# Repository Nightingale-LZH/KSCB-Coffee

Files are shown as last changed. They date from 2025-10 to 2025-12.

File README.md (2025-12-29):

# Precision Cold Drip Coffee Maker

Alternative Interpretation of Kyoto-Style Cold Brew.

Name the coffee maker as Precision Cold Drip (still looking for better name).

## Bill of Material

### 3D-Printed Parts

The project file (.3mf) for [PrusaSlicer](https://www.prusa3d.com/page/prusaslicer_424/) are provided.

- Cold brew machine: [KSCB-3DModel/KSCB-PrusaSlicer.3mf](KSCB-3DModel/KSCB-PrusaSlicer.3mf)
- Cold brew machine case: [KSCB-3DModel/KSCB-Case-PrusaSlicer.3mf](KSCB-3DModel/KSCB-Case-PrusaSlicer.3mf)
- [Optional] STEP file for blank front place for modification: [KSCB-3DModel/BlankFrontPlate.step](KSCB-3DModel/BlankFrontPlate.step)

### Pruchased Parts

Note: in case the exact components cannot be sourced, a [STEP file](KSCB-3DModel/BlankFrontPlate.step) of blank front plate is provided for modification in `KSCB-3DModel` folder.

- **Buck-Boost Converter** (x1)
  - Any boost converter that convert 5V to 12V works. The current requirement is 1A at 12V, but regular operating amperage should never exceed that.
- **Motor Controller** (x1)
  - L298N should suffice. Other equivalent should also work.
  - PWM capability is not required. I found the PWM is not reliable enough and often stall the peristaltic pump. So, short pulsing is more consistent than continuous dripping using PWM.
  - The 5V power supply is not necessary either. If the voltage of the main power source is stable (this is often true from power bank), it can directly power the microcontroller and other 5V devices.
- **7 Segmented Display** (x1)
  - TM1637 powered module would be the best.
- **Button** (x4)
  - Any normally open momentary switch would work here.
  - The model is based on 7mm panel mount buttons.
- **LED** and **Resistor** (x5)
  - The most basic LED will work here.
  - The resistor is for current limiting. The resistance ranging from 200 ohm to 400 ohm would work. 
- **Arduino Nano** (x1)
  - Any microcontroller would work here with pinout modification. The libraries in the code are based on Arduino Framework, and written with PlatformIO extension in VSCode.
  - The code is based on Arduino Nano, and would work without any modification.
- **Peristaltic Pump** (x1)
  - A 12V small peristaltic pump with tube size 3mm ID x 5mm OD would work here. The link to the purchase page is likely to expire in the future, so source the similar item. The picture of the pump used in this build is [here](Others/PumpScreenshot.png). 

## Pump Pulse Flow Rate Calibration Data

function of best fit: 

$$R(t) = 0.000513 e^{-0.009825t} + 0.001392$$

- $t$ is the duration of pulse in milliseconds
- $R$ is the pump flow rate in grams per millisecond

The flow rate is calculated with supply voltage of 12V to L298N module. The voltage received by pump motor is around 10V according to L298N datasheet (voltage drop is around 2V).

See more detail in [KSCB-PumpCalibrationData/PumpTesting.ipynb](KSCB-PumpCalibrationData/PumpTesting.ipynb).

## System Reference Diagram

### Block Diagram

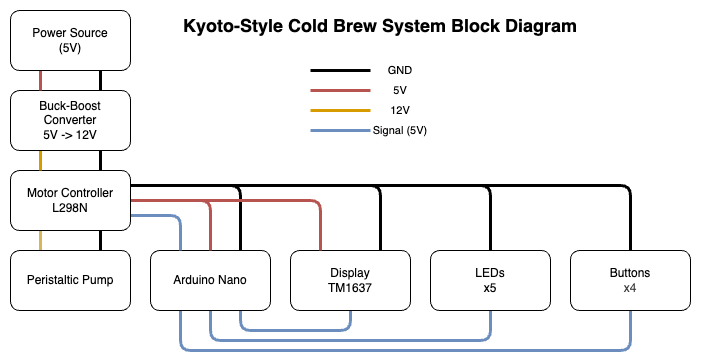
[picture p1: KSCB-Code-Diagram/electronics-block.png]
Block Diagram


### System Finite State Machine

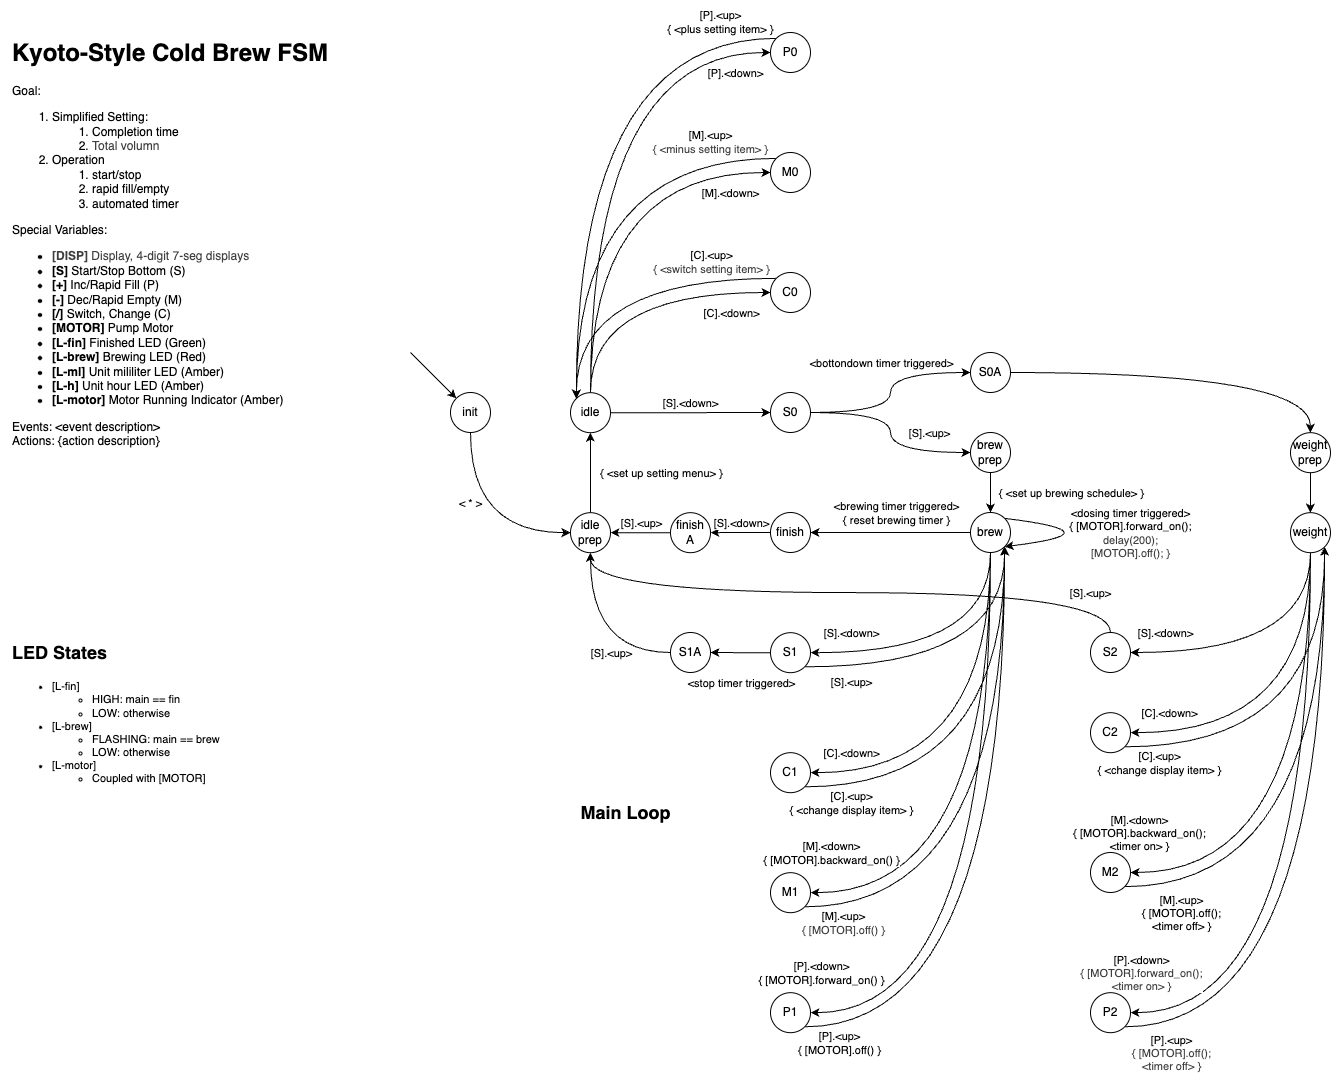
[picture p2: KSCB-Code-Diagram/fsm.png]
System Finite State Machine


## TODO

- [x] Bill of Material
- [ ] Building Guide
- [x] Model parts
- [ ] Circuit Diagram / Schematics
- [x] Calibration code/data
- [x] Control Code
- [ ] User Manual

## Credit

**Zihui(Andy) Liu** ([Personal Website](https://nightingale-lzh.github.io), [GitHub](<https://github.com/Nightingale-LZH>))

This project is published under GNU General Public License version 3 (GPLv3) which allows users to run, modify, and distribute software while ensuring that any modified versions remain open source. This project is funded by creator's love to coffee.

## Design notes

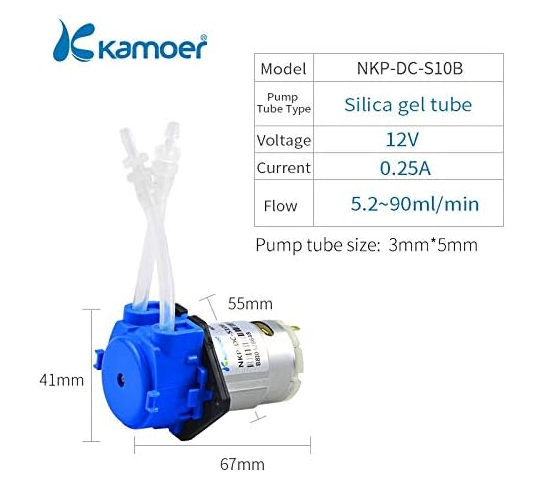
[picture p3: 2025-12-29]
Others/PumpScreenshot.png

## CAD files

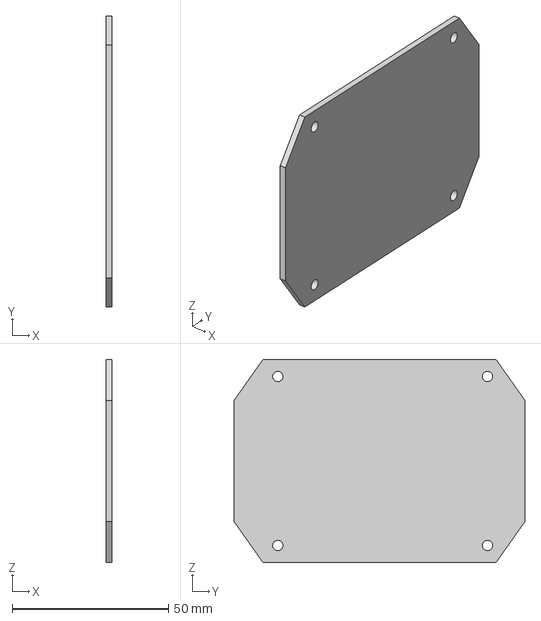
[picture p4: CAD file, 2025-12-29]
KSCB-3DModel/BlankFrontPlate.step
2.00 x 93.0 x 65.0 mm

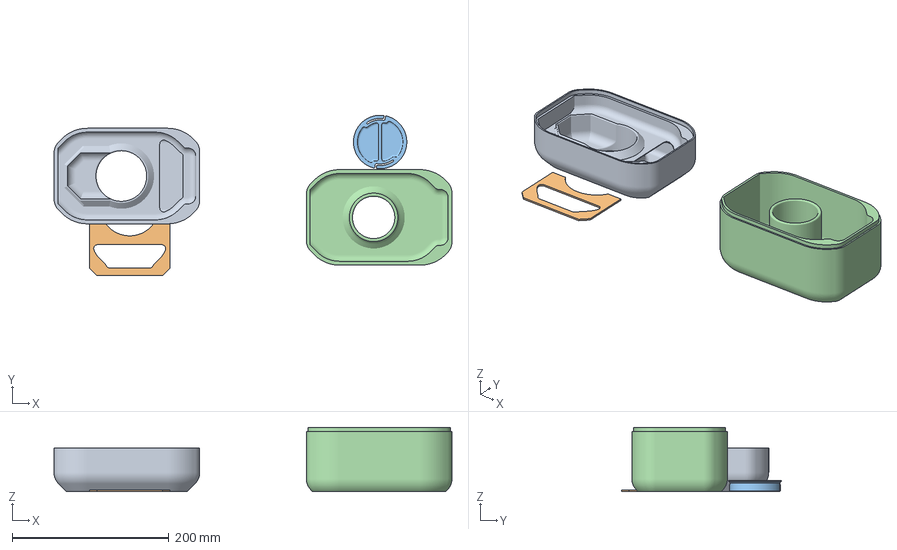
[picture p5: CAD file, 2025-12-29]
KSCB-3DModel/KSCB-Case-PrusaSlicer.3mf
508.1 x 204.8 x 82.0 mm
V1 EC Top.stl
V1 Top Insert.stl
V1 Vent Cap.stl
V1 EC Base.stl

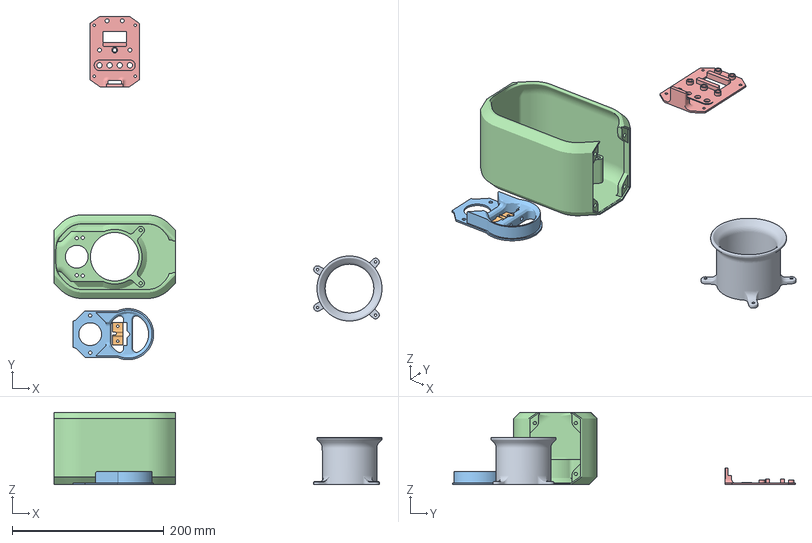
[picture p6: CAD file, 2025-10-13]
KSCB-3DModel/KSCB-PrusaSlicer.3mf
432.3 x 452.6 x 95.0 mm
V1 InnerTube.stl
V1 OverhangBrace.stl
V1 OverhangInsert.stl
V1 Shell.stl
V1 FrontPlateLayout1.stl

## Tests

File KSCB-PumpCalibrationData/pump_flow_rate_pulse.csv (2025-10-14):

on_delay_ms | n_pulse | weight_g
100 | 20 | 3.25
200 | 20 | 5.80
300 | 20 | 8.54
400 | 20 | 11.05
500 | 20 | 13.88
600 | 20 | 16.5
700 | 20 | 19.4
800 | 20 | 22.00
900 | 20 | 24.56
1000 | 20 | 27.00
100 | 40 | 6.11
200 | 40 | 10.8
200 | 40 | 11.69
300 | 40 | 17.28
100 | 40 | 6.26
100 | 40 | 6.85
100 | 40 | 6.27
200 | 40 | 11.52
200 | 40 | 10.75
200 | 40 | 11.25
300 | 40 | 17.34
300 | 40 | 17.39
300 | 40 | 16.9
400 | 20 | 11.26
400 | 20 | 11
400 | 20 | 11.25
400 | 20 | 10.78
500 | 20 | 14.10
500 | 20 | 13.7
500 | 20 | 14.12
500 | 20 | 14.07
600 | 20 | 16.92
600 | 20 | 16.6
600 | 20 | 16.82
600 | 20 | 16.17
700 | 20 | 18.90
700 | 20 | 19.52
700 | 20 | 19.64
700 | 20 | 19.42
800 | 20 | 21.25
800 | 20 | 22.19
800 | 20 | 22.33
800 | 20 | 22.76
900 | 20 | 26.12
900 | 20 | 25.50
900 | 20 | 25.66
900 | 20 | 25.80
1000 | 20 | 29.00
1000 | 20 | 28.45
1000 | 20 | 28.46
1000 | 20 | 28.42
150 | 40 | 9.14
150 | 40 | 9.15
150 | 40 | 9.10
150 | 40 | 9.05
150 | 40 | 9.16
50 | 40 | 3.50
50 | 40 | 3.60
50 | 40 | 3.40
50 | 40 | 3.42
50 | 40 | 3.34
25 | 40 | 1.75
25 | 40 | 1.88
25 | 40 | 1.68
25 | 40 | 1.75
25 | 40 | 1.82
250 | 40 | 14.47
250 | 40 | 14.65
250 | 40 | 14.46
250 | 40 | 14.50
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

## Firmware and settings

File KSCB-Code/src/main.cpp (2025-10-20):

#include "main.h"

#ifdef MAIN

void setup() {}

void loop() {
    main_loop_update();
    built_in_led_update();
    display_manager.update();
    pump_manager.update();

    delay(FSM_DELAY_MS);
}


//  +---------------------------------------------------------------------------------------------+
//  |                                          Main Loop                                          |
//  +---------------------------------------------------------------------------------------------+


void main_loop_update() {
    SETUP_FSM_FUNCTION(main_loop);

    STATE(ML_init) {
        display_manager.show_segment(SEG_PCD);
        SLEEP_TO(1000, ML_init_2);
    }

    STATE(ML_init_2) {
        display_manager.show_segment(SEG_ZLIU);
        SLEEP_TO(1500, ML_idle_prep);
    }

    //  ------- Idle -------
    STATE(ML_idle_prep) {
        pump_manager.end_schedule();
        display_manager.show_segment(SEG_empty_str);
        SLEEP_TO(500, ML_idle_prep_2);
    }

    STATE(ML_idle_prep_2) {
        pump_manager.end_schedule();
        display_manager.show_segment(SEG_PREP);
        SLEEP_TO(1000, ML_idle_prep_3);
    }

    STATE(ML_idle_prep_3) {
        //  Setting up menu
        is_setting_volumn = false;
        is_setting_time = true;

        refresh_display_menu();
        TO(ML_idle);
    }

    STATE(ML_idle) {
        refresh_display_menu_scheduled();
        WHEN(btn_change.is_pressed()) TO(ML_C0);
        WHEN(btn_plus  .is_pressed()) TO(ML_P0);
        WHEN(btn_minus .is_pressed()) TO(ML_M0);
        WHEN(btn_start .is_pressed()) { 
            display_manager.show_segment(SEG_BREW);
            RESET_TIMER(main_loop); 

            TO(ML_S0); 
        }
    }

    STATE(ML_C0) {
        WHEN(btn_change.is_released()) {
            //  switching setting item
            if (is_setting_volumn) {
                is_setting_volumn = false;
                is_setting_time = true;

            } else if (is_setting_time) {
                is_setting_volumn = true;
                is_setting_time = false;
            }

            refresh_display_menu();
            TO(ML_idle)
        }
    }

    STATE(ML_P0) {
        WHEN(btn_plus.is_released()) {
            //  plus setting item
            if (is_setting_volumn) {
                if (brewing_volumn_ml + BREWING_VOLUMN_INCREMENT_ML < 9999) {
                    brewing_volumn_ml += BREWING_VOLUMN_INCREMENT_ML;
                }
            } else if (is_setting_time) {
                if (brewing_time_mins + BREWING_TIME_INCREMENT_MINS < 99 * 60) {
                    brewing_time_mins += BREWING_TIME_INCREMENT_MINS;
                }
            }

            refresh_display_menu();
            TO(ML_idle)
        }
    }

    STATE(ML_M0) {
        WHEN(btn_minus.is_released()) {
            //  minus setting item
            if (is_setting_volumn) {
                if (brewing_volumn_ml - BREWING_VOLUMN_INCREMENT_ML > 0) {
                    brewing_volumn_ml -= BREWING_VOLUMN_INCREMENT_ML;
                }
            } else if (is_setting_time) {
                if (brewing_time_mins - BREWING_TIME_INCREMENT_MINS > 0) {
                    brewing_time_mins -= BREWING_TIME_INCREMENT_MINS;
                }
            }

            refresh_display_menu();
            TO(ML_idle)
        }
    }

    STATE(ML_S0) {
        WHEN(btn_start.is_released()) TO(ML_brew_prep);
        WHEN(IS_TIME_ELAPSED(main_loop, 3000)) {
            display_manager.show_segment(SEG_CALI);
            TO(ML_S0A);
        }
    }

    STATE(ML_S0A) {
        WHEN(btn_start.is_released()) TO(ML_weight_prep);
    }

    //  ------- Brewing -------

    STATE(ML_brew_prep) {
        //  setup brewing schedule
        long brewing_total_time_ms = brewing_time_mins * 60 * 1000;

        is_showing_brewing_time_left = true;
        is_showing_brewing_volumn_left = false;

        pump_manager.start_schedule(brewing_total_time_ms, brewing_volumn_ml);
        //  manually trigger time once to activate flashing dots
        display_manager.show_time_min(pump_manager.get_brewing_time_remaining_mim(), true, true);
        refresh_display_brewing();

        TO(ML_brew)
    }

    STATE(ML_brew) {
        refresh_display_brewing_scheduled();

        WHEN(btn_change.is_pressed()) TO(ML_C1);
        WHEN(btn_plus  .is_pressed()) { pump_manager.override_forward_on();  TO(ML_P1); }
        WHEN(btn_minus .is_pressed()) { pump_manager.override_backward_on(); TO(ML_M1); }
        WHEN(btn_start .is_pressed()) { 
            display_manager.show_segment(SEG_HOLD);
            RESET_TIMER(main_loop);     

            TO(ML_S1); 
        }
        WHEN(pump_manager.is_brewing_finished()) { 
            display_manager.show_segment(SEG_FIN);
            pump_manager.end_schedule(); 
            pump_manager.backward_on();

            SLEEP_TO(ML_finish, 15000); 
        }
    }

    STATE(ML_C1) { 
        refresh_display_brewing_scheduled();

        WHEN(btn_change.is_released()) {
            //  switching setting item
            if (is_showing_brewing_volumn_left) {
                is_showing_brewing_volumn_left = false;
                is_showing_brewing_time_left = true;

            } else if (is_showing_brewing_time_left) {
                is_showing_brewing_volumn_left = true;
                is_showing_brewing_time_left = false;
            }

            refresh_display_brewing();
            TO(ML_brew)
        }
    }

    STATE(ML_P1) {
        refresh_display_brewing_scheduled();

        WHEN(btn_plus.is_released()) {
            pump_manager.override_off();
            pump_manager.end_override();

            refresh_display_brewing();
            TO(ML_brew)
        }
    }

    STATE(ML_M1) {
        refresh_display_brewing_scheduled();

        WHEN(btn_minus.is_released()) {
            pump_manager.override_off();
            pump_manager.end_override();

            refresh_display_brewing();
            TO(ML_brew)
        }
    }

    STATE(ML_S1) {
        WHEN(btn_start.is_released()) {
            refresh_display_brewing();

            TO(ML_brew);
        }
        WHEN(IS_TIME_ELAPSED(main_loop, 3000)) { 
            display_manager.show_segment(SEG_STOP);
            pump_manager.end_schedule(); 

            TO(ML_S1A); 
        }
    }

    STATE(ML_S1A) {
        WHEN(btn_start.is_released()) TO(ML_idle_prep);
    }

    STATE(ML_finish) {
        pump_manager.off();
        led_brew.off();
        led_fin.on();

        TO(ML_finish_2)
    }

    STATE(ML_finish_2) {
        WHEN(btn_start.is_pressed()) TO(ML_finish_A);
    }

    STATE(ML_finish_A) {
        WHEN(btn_start.is_released()) TO(ML_idle_prep);
    }

    //  ------- Weighting -------

    STATE(ML_weight_prep) {
        curr_volumn_ul = 0;
        refresh_display_meansuring(curr_volumn_ul);

        TO(ML_weight)
    }

    STATE(ML_weight) {
        refresh_display_meansuring_scheduled(curr_volumn_ul);

        WHEN(btn_change.is_pressed()) TO(ML_C2);

        WHEN(btn_plus  .is_pressed()) { 
            pump_manager.override_forward_on();  
            RESET_TIMER(main_loop_measuring); 
            
            TO(ML_P2); 
        }

        WHEN(btn_minus .is_pressed()) { 
            pump_manager.override_backward_on(); 
            RESET_TIMER(main_loop_measuring); 

            TO(ML_M2); 
        }

        WHEN(btn_start .is_pressed()) TO(ML_S2);
    }

    STATE(ML_C2) { 
        WHEN(btn_change.is_released()) {
            curr_volumn_ul = 0;
            refresh_display_meansuring(curr_volumn_ul);

            TO(ML_weight)
        }
    }

    STATE(ML_P2) {
        refresh_display_meansuring_scheduled(
            curr_volumn_ul + PumpStats::ms2ul(TIME_ELAPSED(main_loop_measuring))
        );

        WHEN(btn_plus.is_released()) {
            pump_manager.override_off();
            curr_volumn_ul += PumpStats::ms2ul(TIME_ELAPSED(main_loop_measuring));
            pump_manager.end_override();
            refresh_display_meansuring(curr_volumn_ul);

            TO(ML_weight)
        }
    }

    STATE(ML_M2) {
        refresh_display_meansuring_scheduled(
            curr_volumn_ul - PumpStats::ms2ul(TIME_ELAPSED(main_loop_measuring))
        );

        WHEN(btn_minus.is_released()) {
            pump_manager.override_off();
            curr_volumn_ul -= PumpStats::ms2ul(TIME_ELAPSED(main_loop_measuring));
            pump_manager.end_override();
            refresh_display_meansuring(curr_volumn_ul);

            TO(ML_weight)
        }
    }

    STATE(ML_S2) {
        WHEN(btn_start.is_released()) TO(ML_idle_prep);
    }
}

//  +---------------------------------------------------------------------------------------------+
//  |                                       Helper Function                                       |
//  +---------------------------------------------------------------------------------------------+

void refresh_display_menu() {
    if (is_setting_volumn) {
        display_manager.show_ml(brewing_volumn_ml);
    } else if (is_setting_time) {
        display_manager.show_time_min(brewing_time_mins, true, false);
    }

    led_brew.off();
    led_fin.off();
}

void refresh_display_menu_scheduled() {
    if (!IS_TIME_ELAPSED(refresh_display_menu_scheduled_timer, 500)) {
        return;
    } 
    RESET_TIMER(refresh_display_menu_scheduled_timer); 

    refresh_display_menu();
}

void refresh_display_brewing() {
    if (is_showing_brewing_time_left) {
        long time_remaining_min = pump_manager.get_brewing_time_remaining_mim();
        if (time_remaining_min < 0) { 
            time_remaining_min = 0;
            display_manager.show_time_min(0, true, false);
        }

        if (display_manager.is_showing_hr_min()) {
            display_manager.update_time_min(time_remaining_min);
        } else {
            //  now showing the time, then call the function to reset
            display_manager.show_time_min(time_remaining_min, true, true);
        }

    } else if (is_showing_brewing_volumn_left) {
        display_manager.show_ml(pump_manager.get_brewing_volumn_remaining_ml());
    }

    led_brew.on();
    led_fin.off();
}

void refresh_display_brewing_scheduled() {
    if (!IS_TIME_ELAPSED(refresh_display_brewing_scheduled_timer, 500)) {
        return;
    } 
    RESET_TIMER(refresh_display_brewing_scheduled_timer); 

    refresh_display_brewing();
}

void refresh_display_meansuring(long volumn_ul) {
    display_manager.show_ml(volumn_ul / 1000);
    led_brew.on();
    led_fin.on();
}

void refresh_display_meansuring_scheduled(long volumn_ul) {
    if (!IS_TIME_ELAPSED(refresh_display_meansuring_scheduled_timer, 100)) {
        return;
    } 
    RESET_TIMER(refresh_display_meansuring_scheduled_timer); 

    refresh_display_meansuring(volumn_ul);
}

//  +---------------------------------------------------------------------------------------------+
//  |                                        Autonomous                                           |
//  +---------------------------------------------------------------------------------------------+

void built_in_led_update() {
    SETUP_FSM_FUNCTION(builtin_led);

    STATE(0) {
        led_builtin.on();
        SLEEP_TO_NEXT(1000);
    }

    STATE(1) {
        led_builtin.off();
        SLEEP_TO(1000, 0);
    }
}

///////////////////////////////////////////////////////////////////////////////////////////////////
#elif defined(CALIBRATE)

#define ON_DURATION_MS 200
#define OFF_DURATION_MS 500
#define N_PULSE 0

void setup() {
    display.showNumberDec(0);
    
    for (int i = 0; i < N_PULSE; i++) {
        delay(OFF_DURATION_MS);
        pump.forward_on();
        led_motor.on();
        delay(ON_DURATION_MS);
        pump.off();
        led_motor.off();

        display.showNumberDec(i + 1);
    }

    led_fin.on();
}

void loop() {
    if (btn_plus.is_pressed()) {
        pump.forward_on();
        led_motor.on();
    } else if (btn_minus.is_pressed()) {
        pump.backward_on();
        led_motor.on();
    } else {
        pump.off();
        led_motor.off();
    }
    delay(100);
}

///////////////////////////////////////////////////////////////////////////////////////////////////
#elif defined(DEBUG)

//  DEBUG OPTIONS
#define DEBUG_LED
// #define DEBUG_MOTOR
// #define DEBUG_BUTTON
#define DEBUG_DISPLAY

void setup() {
    #ifdef DEBUG_MOTOR
    pinMode(PIN_L298N_ENA, OUTPUT);
    pinMode(PIN_L298N_IN1, OUTPUT);
    pinMode(PIN_L298N_IN2, OUTPUT);

    // Motor Forward Direcction
    digitalWrite(PIN_L298N_IN1, HIGH);
    digitalWrite(PIN_L298N_IN2, LOW);
    #endif  //  DEBUG_MOTOR


    #ifdef DEBUG_LED
    pinMode(PIN_LED_BUILTIN, OUTPUT);
    pinMode(PIN_LED_BREW  , OUTPUT);
    pinMode(PIN_LED_FIN   , OUTPUT);
    pinMode(PIN_LED_MOTOR , OUTPUT);
    pinMode(PIN_LED_ML    , OUTPUT);
    pinMode(PIN_LED_HR_MIN, OUTPUT);
    #endif  //  DEBUG_LED


    #ifdef DEBUG_BUTTON
    Serial.begin(9600);
    pinMode(PIN_BTN_CHANGE, INPUT_PULLUP);
    pinMode(PIN_BTN_START , INPUT_PULLUP);
    pinMode(PIN_BTN_PLUS  , INPUT_PULLUP);
    pinMode(PIN_BTN_MINUS , INPUT_PULLUP);
    #endif  //  DEBUG_BUTTON


    #ifdef DEBUG_DISPLAY
    
    #endif  //  DEBUG_DISPLAY
}

void loop() {
    #ifdef DEBUG_MOTOR
    digitalWrite(PIN_L298N_ENA, LOW);
    delay(2500);

    digitalWrite(PIN_L298N_ENA, HIGH);
    delay(500);
    #endif  //  DEBUG_MOTOR


    #ifdef DEBUG_LED
    digitalWrite(PIN_LED_BUILTIN, HIGH);
    digitalWrite(PIN_LED_BREW  , HIGH);
    delay(1000);
    digitalWrite(PIN_LED_FIN   , HIGH);
    delay(1000);
    digitalWrite(PIN_LED_MOTOR , HIGH);
    delay(1000);
    digitalWrite(PIN_LED_HR_MIN, HIGH);
    delay(1000);
    digitalWrite(PIN_LED_ML    , HIGH);
    delay(1000);

    digitalWrite(PIN_LED_BUILTIN, LOW);
    digitalWrite(PIN_LED_BREW  , LOW);
    digitalWrite(PIN_LED_FIN   , LOW);
    digitalWrite(PIN_LED_MOTOR , LOW);
    digitalWrite(PIN_LED_ML    , LOW);
    digitalWrite(PIN_LED_HR_MIN, LOW);
    delay(1000);
    #endif  //  DEBUG_LED


    #ifdef DEBUG_BUTTON
    if (!digitalRead(PIN_BTN_CHANGE)) { Serial.println("CHANGE"); }
    if (!digitalRead(PIN_BTN_START )) { Serial.println("START"); }
    if (!digitalRead(PIN_BTN_PLUS  )) { Serial.println("PLUS"); }
    if (!digitalRead(PIN_BTN_MINUS )) { Serial.println("MINUS"); }
    Serial.println("---");
    delay(1000);
    #endif  //  DEBUG_BUTTON


    #ifdef DEBUG_DISPLAY
    display.setBrightness(0x0f);

    display.showNumberDecEx(0000, TM1637_DOT_BYTECODE);
    delay(500);
    display.showNumberDecEx(1111);
    delay(500);
    display.showNumberDecEx(2222, TM1637_DOT_BYTECODE);
    delay(500);
    display.showNumberDecEx(3333);
    delay(500);
    display.showNumberDecEx(4444, TM1637_DOT_BYTECODE);
    delay(500);
    display.showNumberDecEx(5555);
    delay(500);
    display.showNumberDecEx(6666, TM1637_DOT_BYTECODE);
    delay(500);
    display.showNumberDecEx(7777);
    delay(500);
    display.showNumberDecEx(8888, TM1637_DOT_BYTECODE);
    delay(500);
    display.showNumberDecEx(9999);
    delay(500);
    #endif  //  DEBUG_DISPLAY
}
#endif // DEBUG_IO

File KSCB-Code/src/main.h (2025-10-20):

#ifndef __MAIN_H__
#define __MAIN_H__

#include "Arduino.h"

#include "FSMMacroV2.h"
#include "TimerMacroV2.h"

#include "LEDSimple.h"
#include "ButtonSimple.h"

#include "TM1637Display.h"
#include "DisplayManager.h"

#include "L298NSingle.h"
#include "PumpManager.h"
#include "PumpScheduler.h"
#include "PumpStats.h"

#define MAIN
// #define DEBUG
// #define CALIBRATE

//  +---------------------------------------------------------------------------------------------+
//  |                                              IO                                             |
//  +---------------------------------------------------------------------------------------------+

#define FSM_DELAY_MS 5

#define PIN_LED_BUILTIN 13

#define PIN_LED_BREW    6
#define PIN_LED_FIN     5
#define PIN_LED_MOTOR   4
#define PIN_LED_HR_MIN  3
#define PIN_LED_ML      2

#define PIN_BTN_CHANGE  14
#define PIN_BTN_START   17
#define PIN_BTN_PLUS    15
#define PIN_BTN_MINUS   16

#define PIN_L298N_ENA   11
#define PIN_L298N_IN1   10
#define PIN_L298N_IN2   9

#define PIN_TM1637_DIO  12
#define PIN_TM1637_CLK  7

#define TM1637_DOT_BYTECODE 0b01000000

LED led_builtin (PIN_LED_BUILTIN );
LED led_brew    (PIN_LED_BREW    );
LED led_fin     (PIN_LED_FIN     );
LED led_motor   (PIN_LED_MOTOR   );
LED led_ml      (PIN_LED_ML      );
LED led_hr_min  (PIN_LED_HR_MIN  );

Button btn_change(PIN_BTN_CHANGE);
Button btn_start (PIN_BTN_START );
Button btn_plus  (PIN_BTN_PLUS  );
Button btn_minus (PIN_BTN_MINUS );

TM1637Display display(PIN_TM1637_CLK, PIN_TM1637_DIO);
DisplayManager display_manager(&display, &led_ml, &led_hr_min, TM1637_DOT_BYTECODE);

L298NSingle pump(PIN_L298N_ENA, PIN_L298N_IN1, PIN_L298N_IN2);

PumpScheduler_ConstantNumPulse pump_scheduler(1000);
PumpManager pump_manager(&pump, &led_motor, &pump_scheduler);


//  +---------------------------------------------------------------------------------------------+
//  |                                       Internal States                                       |
//  +---------------------------------------------------------------------------------------------+

//  --- menu ---

#define BREWING_VOLUMN_INCREMENT_ML 50
#define BREWING_TIME_INCREMENT_MINS 30

long brewing_volumn_ml = 500;
long brewing_time_mins = 480;

bool is_setting_volumn = true;
bool is_setting_time = false;

//  --- brewing sequence ---

bool is_showing_brewing_volumn_left = true;
bool is_showing_brewing_time_left = false;

//  --- measuring sequence ---

long curr_volumn_ul = 0;


//  +---------------------------------------------------------------------------------------------+
//  |                                          Main Loop                                          |
//  +---------------------------------------------------------------------------------------------+

enum FSM_Main_Loop {
    ML_init, ML_init_2, 
    ML_idle_prep, ML_idle_prep_2, ML_idle_prep_3, ML_idle, 
    ML_S0, ML_S0A, ML_C0, ML_M0, ML_P0, 
    ML_brew_prep, ML_brew, 
    ML_S1, ML_S1A, ML_C1, ML_M1, ML_P1,
    ML_finish, ML_finish_2, ML_finish_A, 
    ML_weight_prep, ML_weight,
    ML_S2, ML_S2A, ML_C2, ML_M2, ML_P2
};
FSM_Main_Loop state_main_loop = ML_init;

CREATE_FSM(main_loop, ML_init);
CREATE_TIMER(main_loop)
CREATE_TIMER(main_loop_measuring)
void main_loop_update();

//  +---------------------------------------------------------------------------------------------+
//  |                                  Display Strings Constants                                  |
//  +---------------------------------------------------------------------------------------------+

uint8_t SEG_empty_str[] = {0, 0, 0, 0};

uint8_t SEG_ZLIU[] = {
    SEG_A | SEG_B | SEG_G | SEG_E | SEG_D,          //  Z
    SEG_F | SEG_E | SEG_D,                          //  L
    SEG_F | SEG_E,                                  //  I
    SEG_F | SEG_E | SEG_D | SEG_D | SEG_C | SEG_B   //  U
};

uint8_t SEG_PCD[] = {
    SEG_A | SEG_B | SEG_F | SEG_G | SEG_E,  //  P
    SEG_A | SEG_F | SEG_E | SEG_D,          //  C
    SEG_B | SEG_C | SEG_D | SEG_E | SEG_G,  //  d
    0
};

uint8_t SEG_FIN[] = {
    SEG_A | SEG_F | SEG_G | SEG_E,      //  F
    SEG_F | SEG_E,                      //  I
    SEG_E | SEG_G | SEG_C,              //  n
    0
};

uint8_t SEG_STOP[] = {
    SEG_A | SEG_F | SEG_G | SEG_C | SEG_D,          //  S
    SEG_F | SEG_G | SEG_E | SEG_D,                  //  t
    SEG_A | SEG_B | SEG_C | SEG_D | SEG_E | SEG_F,  //  O
    SEG_A | SEG_B | SEG_F | SEG_G | SEG_E           //  P
};

uint8_t SEG_BREW[] = {
    SEG_F | SEG_G | SEG_E | SEG_D | SEG_C,  //  b
    SEG_G | SEG_E,                          //  r
    SEG_A | SEG_F | SEG_G | SEG_E | SEG_D,  //  E
    SEG_E | SEG_D | SEG_C                   //  u
};
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

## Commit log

2025-10-07 Added 3d printing file, updated FSM
    [KSCB-PrusaSlicer.3mf]
2025-10-13 Finished first pulse test
    [pump_flow_rate_pulse.csv]
2025-10-14 Finished pump flowrate analysis
    [pump_flow_rate_pulse.csv]
2025-10-19 Refactured cold to add pump scheduler, add linear fit directly by volumn
2025-10-19 Finished pump measuring function
2025-12-29 Added BOM
    [BlankFrontPlate.step, KSCB-Case-PrusaSlicer.3mf]
